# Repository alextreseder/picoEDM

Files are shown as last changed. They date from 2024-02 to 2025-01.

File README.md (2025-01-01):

# PicoEDM

Minimalist DIY Wire EDM for Hobbyists & Education. Designed with high accuracy and user experience in mind.

[**Join the Discord!!**](https://discord.gg/fNJQsGFzm4)

[**Pico Makes First Cut!**](https://youtube.com/shorts/JkDtk-GV0A8)

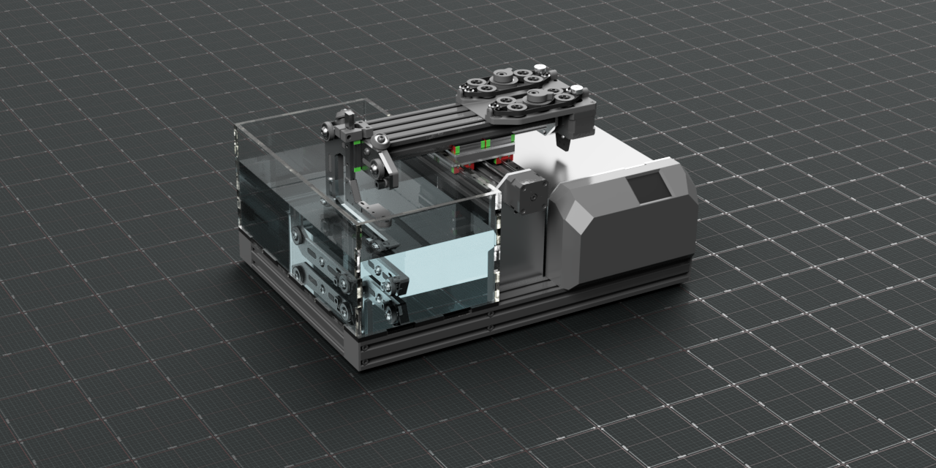
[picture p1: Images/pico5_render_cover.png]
Render Cover


## Concept

* Use components that are readily available worldwide (Amazon.com serving as benchmark)
* 360mm by 500mm footprint and 160mmX; 160mmY; 50mmZ travels
* Use a belted friction drive for wire handling
* Use a integrated driver closed loop stepper in torque mode to tension the wire
* Use inert materials for underwater assemblies
* Implement adjustable worktable for precision
* Use preloaded Tr8x2 nuts with integrated leadscrew steppers and mgn12 rails for motion
* Support the following features via a quick swap kinematic mount:
  * Sinker EDM end effector
  * Hole popper end effector

The firmware and spark generator is a seperate project supplied by
[GEDM](https://github.com/G-EDM)

## Project Status
```diff
+ PROJECT NOW IN BETA! CURRENT VERSION: PICO7
```
## Disclaimers

**EDM machines are dangerous**  
Beware electric shock and pinch points. Be prepared to activate emergency stop. Do not leave machine unattended. You are responsible for your own safety.

**Metric / Imperial**
The machine is nearly completely metric with the exception of the thickness of the laser cut parts. The nearest metric equivalents should work in all cases, but user should carefully review the CAD model before building to confirm.

## Currently In Progress

* Implement assited self threading

## Associated Projects
[NanoEDM - A higher quality machine](https://github.com/alextreseder/nanoEDM)

[KegStand - A consumables free water management system for EDM](https://github.com/alextreseder/kegstand)

## Future Goals
Future Development:
* Ultra-compact spark generator based on FGPA control technology

## Non-Goals
This is not a spark generator or firmware project, although I do have a high end spark generator under development. This is not an ultra precision machine. This is not a low precision machine.

## Calculations
Desmos calculators have been made for various applications - they are not necessarily complete

[DESMOS - CAPSTAN EQUATION](https://www.desmos.com/calculator/trg4qsopa3)

## Donations
Bitcoin address: bc1qqp8etjvsmyyjqjm5unr0l4kj4qqpekz5jcclxv

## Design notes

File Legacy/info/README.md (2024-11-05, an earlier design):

# Bill Of Materials

## Fabricated Parts

|Part |Source |QTY  |Cost Each |Cost Each (Bulk) |
|---|---|-----|---|---|
|Preload Nut Mount |SendCutSend|2 |$2 |$0.50 |
|Tank Floor Thick Plate|SendCutSend|1 |$66 |$16.00 |
|Tank Floor Thin Plate |SendCutSend|1 |$28 |$7 |
|Wire Frame |SendCutSend|1 |$40 |$12 |
|X Axis Plate |SendCutSend|2 |$18 |$6.00 |
|Tank Walls |Home Laser |1 |$20.00 |$5.00 |
| | | | | |
| | |total|194 |53 |

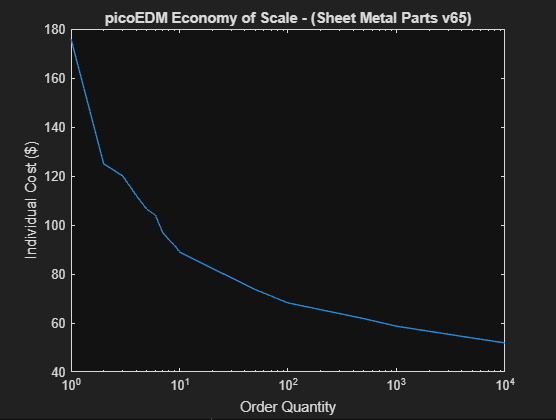
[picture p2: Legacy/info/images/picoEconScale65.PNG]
Economy of Scale


## Sourced Parts

|Part |Source |QTY  |Cost Each |Cost Each (Bulk) |Link|
|---|---|:---:|---:|---:|----|
|608zz Ceramic |Amazon |8 |$2 |$0.50 | |
|608zz Steel |Amazon |8 |$1 |$0.10 | |
|3/4" AL Angle 48" |ACE |2 |$5 |$2 | |
|4040 V-Slot 500mm |Amazon |4 |$15 |$8 | |
|12D 350L Linear Shaft |Amazon |4 |$6 |$1.50 | |
|LM12UU |Amazon |8 |$1.50 |$0.50 | |
|Nema17 Tr8x2 300mm |Amazon |2 |$25 |$10 | |
|MR105-2RS Bearing |Amazon |1 |$0.50 |$0.05 | |
|Tr8x2 Anti-Backlash Nut  |Amazon |2 |$5 |$2 | |
|BTT Dual Gear Extruder |Amazon |1 |$14 |$5 | |
|Nema17 38mm |Amazon |2 |$12 |$8 | |
|MKS Servo42D |Amazon |1 |$25 |$9 | |
|1/2" PVC SCH80 360mm |Home Depot |1 |$4 |$0.50 | |
|Teflon Bowden Kit |Amazon |1 |$12 |$2 | |
|S203 Wire Guide |Ali Express|2 |$20 |$15 | |
|Wire Contacts |Amazon |2 |$3 |$1 | |
|4D 10L Dowel Pins |Amazon |8 |$0.20 |$0.01 | |
|4D Ball Bearings |Amazon |8 |$0.20 |$0.01 | |
|16T 5B GT2 Pulley |Amazon |2 |$3 |$0.50 | |
|5D 12L Dowel Pin |Amazon |1 |$1 |$0.01 | |
|1/2" Rubber Adhesive Feet|Amazon |6 |$1 |$0.01 | |
|1Kg PETG |Amazon |1 |$20 |$15 | |
| | | | | | |
| | |total|347.7 |155.58 | |

## Total

| | 1 | Bulk |
|:----|:---:|:---:|
|Total|$541 |$208 |

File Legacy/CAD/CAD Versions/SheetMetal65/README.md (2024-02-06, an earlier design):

# STATUS

* UP TO DATE v65

# Guide

* .dxf file name = .step file name + verison number
* Nearest metric equivalent thickness is acceptable
* Recommended Supplier (States) [SendCutSend](https://sendcutsend.com/)

## Sheet Metal Table

| Part Name v65| Quantity | Material | Thickness | 
|:---|:---:|:---:|:---:|
|Preload Nut Mount|2|AL5052|0.080"|
|Tank Floor Thick Plate|1|A36|0.250"|
|Tank Floor Thin Plate|1|SS304|0.030"|
|Tank Wall Long|2|Clear Acrylic|0.250"|
|Tank Wall Short|2|Clear Acrylic|0.250"|
|Wire Frame|1|SS304|0.187"|
|X Axis Plate|2|AL5052|0.250"|

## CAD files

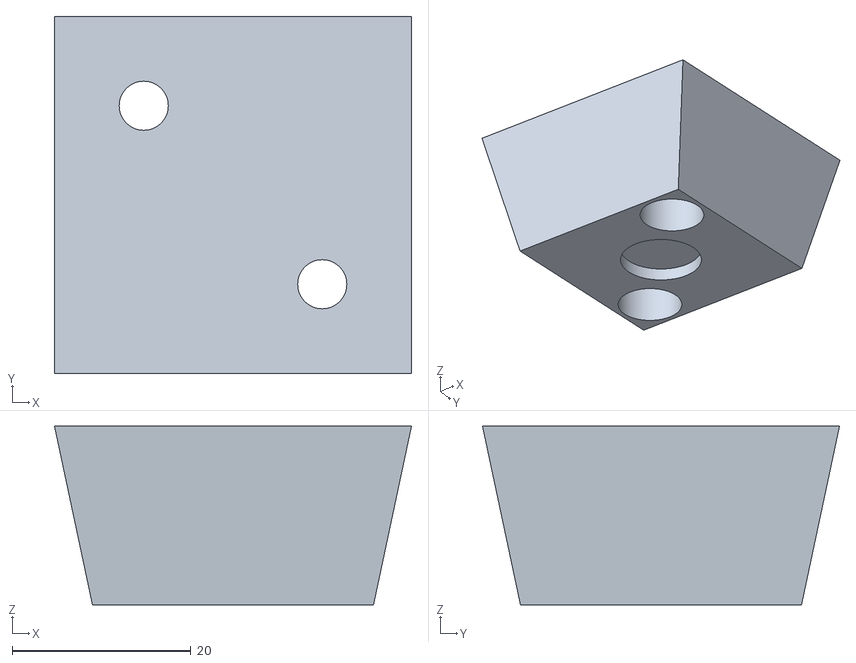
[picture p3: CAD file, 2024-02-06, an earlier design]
Legacy/CAD/CAD Versions/Prints65/MachinePrints65/FootNoHole65.stl
40.0 x 40.0 x 20.0

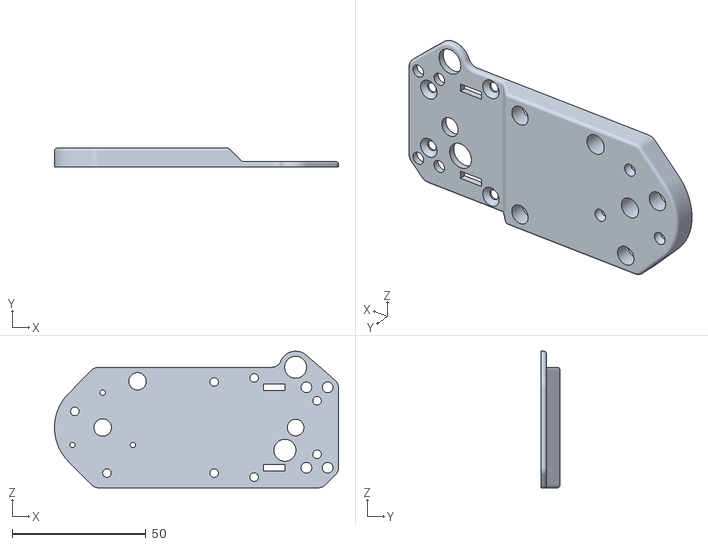
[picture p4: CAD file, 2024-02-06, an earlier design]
Legacy/CAD/CAD Versions/Prints65/WireHandlerPrints65/Bulkhead65.stl
106.0 x 7.00 x 51.0

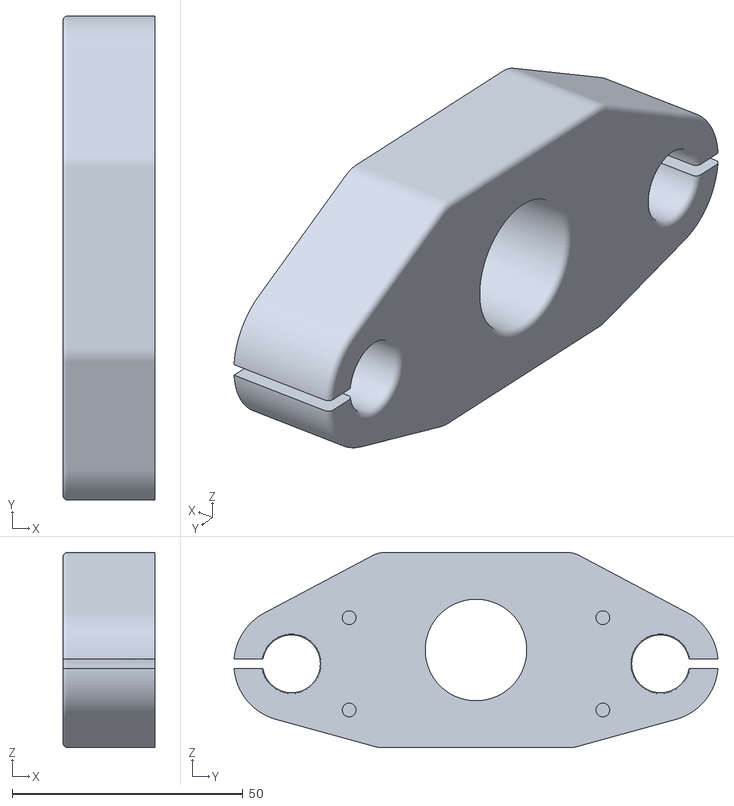
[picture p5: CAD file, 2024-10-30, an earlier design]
Legacy/CAD/CAD Versions/prints66/XbracketBearing66.stl
20.0 x 104.9 x 42.3

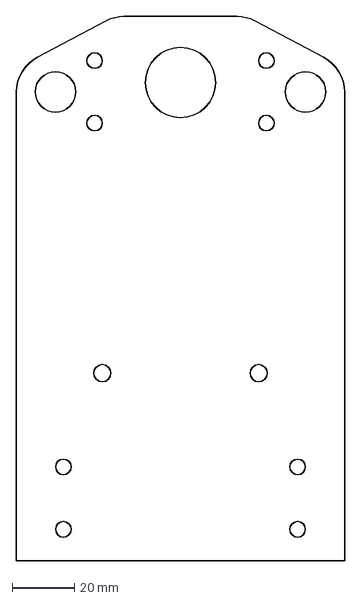
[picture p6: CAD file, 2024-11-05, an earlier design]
Legacy/CAD/CAD Versions/SheetMetal65/XaxisPlate65.dxf
105.0 x 174.2 mm

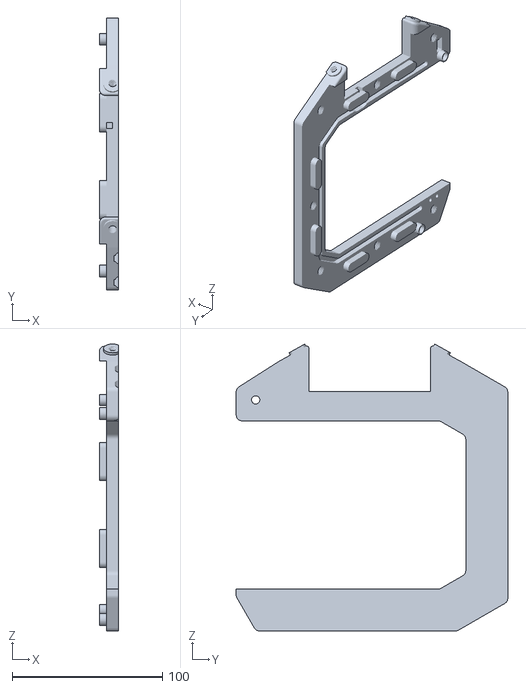
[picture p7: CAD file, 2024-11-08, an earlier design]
Legacy/pico4 prints/End Effector Frame Plastic.stl
12.8 x 181.0 x 191.2

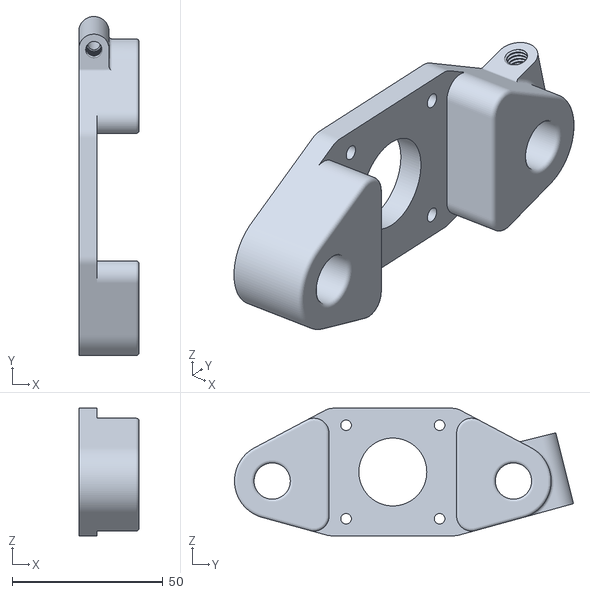
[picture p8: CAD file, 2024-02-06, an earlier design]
Legacy/CAD/CAD Versions/Prints65/MachinePrints65/XbracketMotor65.stl
20.0 x 112.4 x 42.3

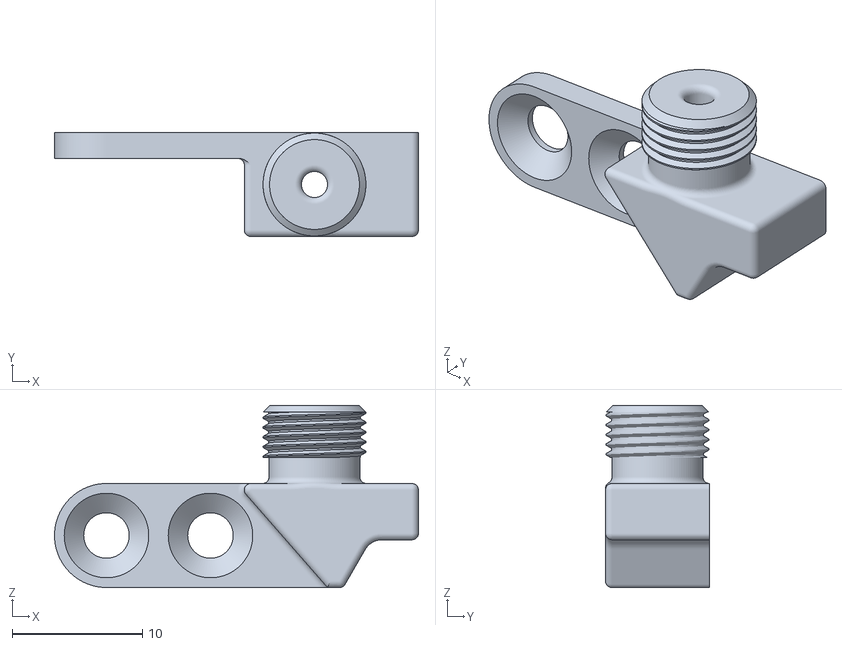
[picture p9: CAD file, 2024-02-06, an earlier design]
Legacy/CAD/CAD Versions/Prints65/WireHandlerPrints65/LowerGuideMount65.stl
28.0 x 8.00 x 14.0

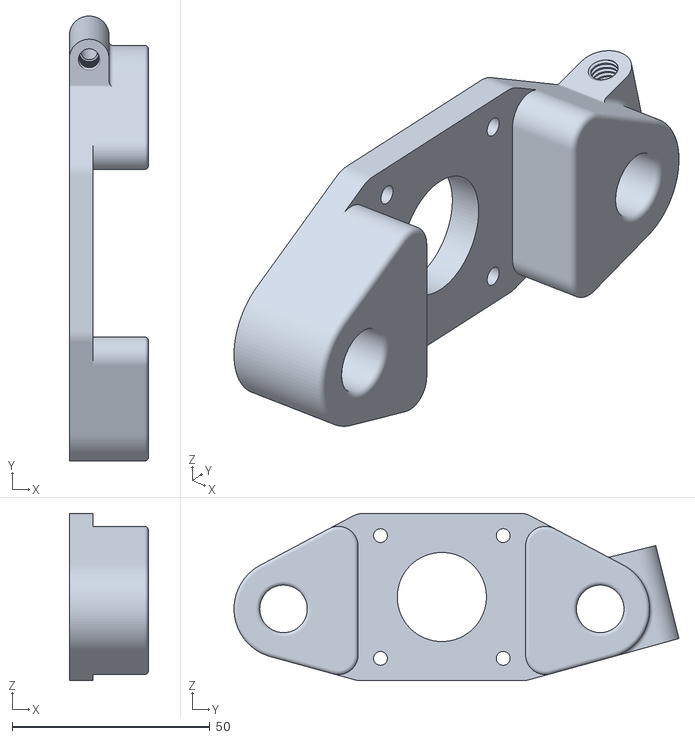
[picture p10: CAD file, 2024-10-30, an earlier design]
Legacy/CAD/CAD Versions/prints66/XbracketMotor66.stl
20.0 x 112.4 x 42.3

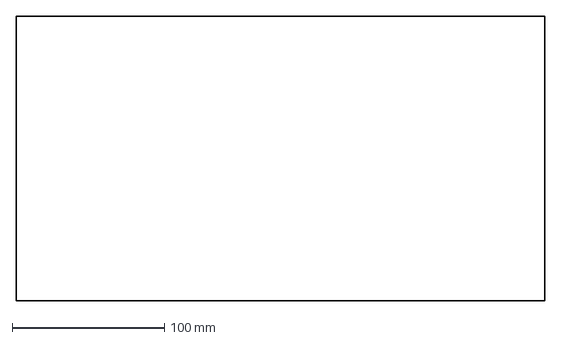
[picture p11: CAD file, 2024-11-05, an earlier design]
Legacy/CAD/CAD Versions/SheetMetal65/TankFloorThinPlate.dxf
347.0 x 187.0 mm

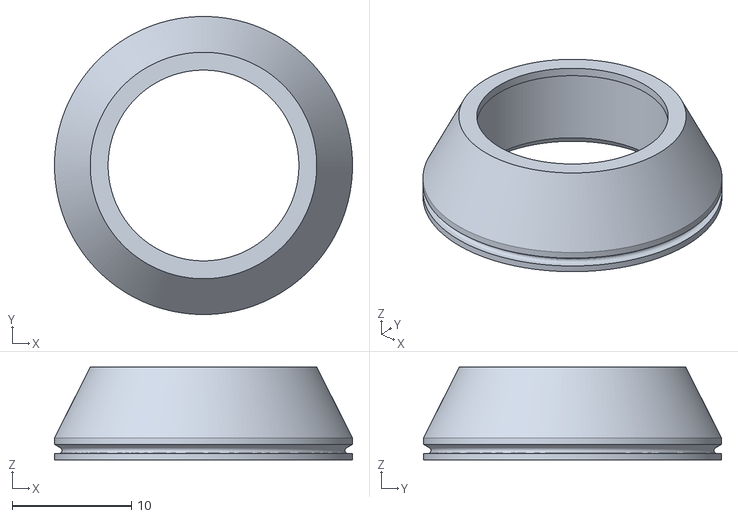
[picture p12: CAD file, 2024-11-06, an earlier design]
Legacy/pico4 prints/606 Groove Ring.stl
25.0 x 25.0 x 7.80

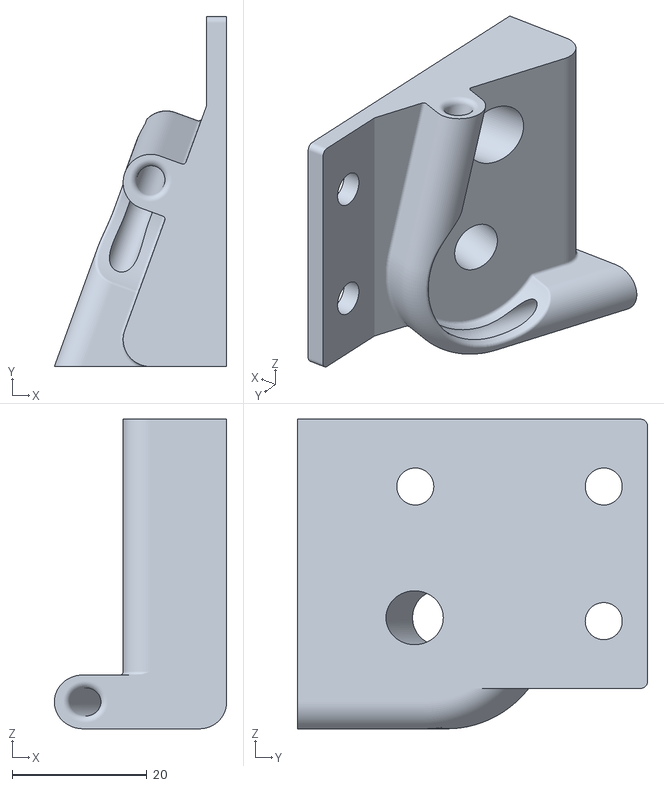
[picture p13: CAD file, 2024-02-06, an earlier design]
Legacy/CAD/CAD Versions/Prints65/MachinePrints65/UnspoolGuideSide65.stl
25.6 x 52.0 x 46.0

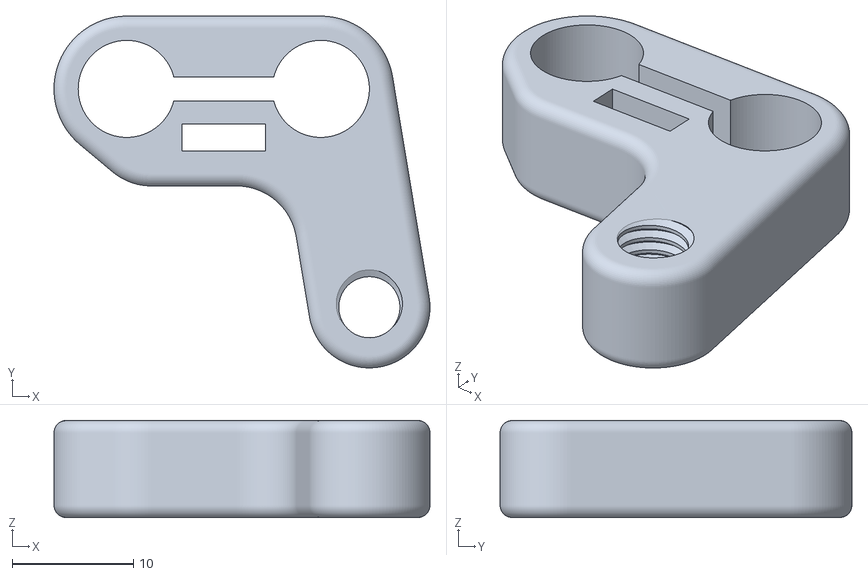
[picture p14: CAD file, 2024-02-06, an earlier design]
Legacy/CAD/CAD Versions/Prints65/WireHandlerPrints65/ZtopConnector65.stl
31.0 x 29.0 x 8.00

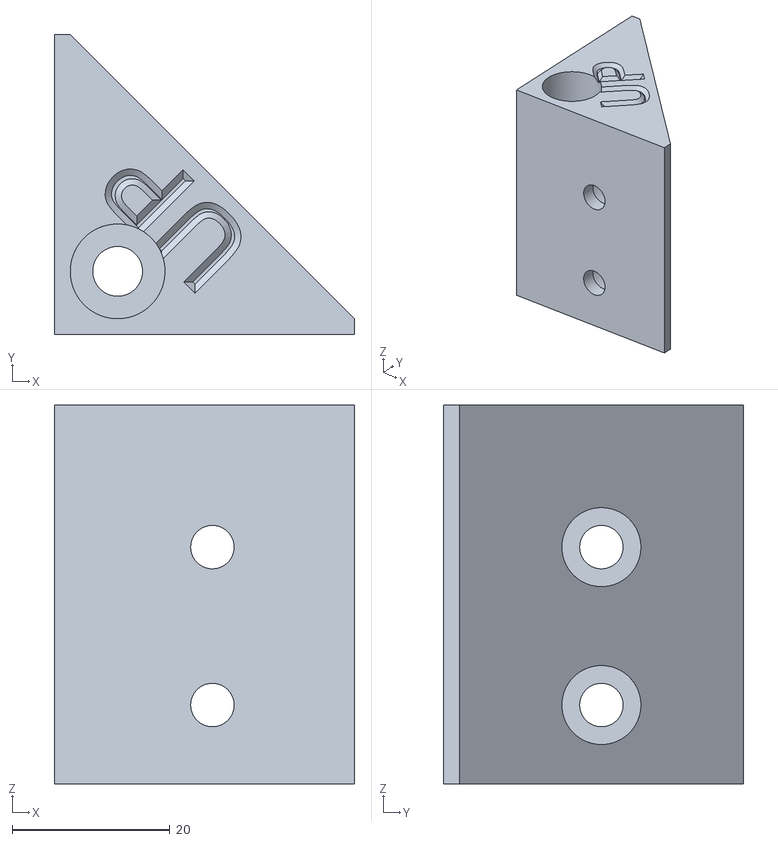
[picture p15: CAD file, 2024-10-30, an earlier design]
Legacy/CAD/CAD Versions/prints66/CornerBrace66.stl
38.0 x 38.0 x 48.0

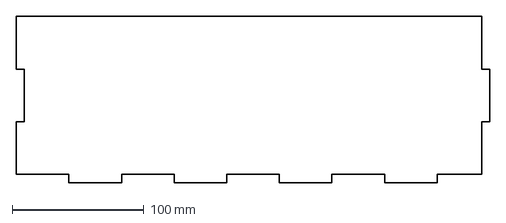
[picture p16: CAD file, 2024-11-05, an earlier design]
Legacy/CAD/CAD Versions/SheetMetal65/TankWallLong.dxf
360.0 x 126.3 mm

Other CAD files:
Legacy/pico4 prints/Lower Guide Mount.stl
Legacy/CAD/CAD Versions/Prints65/MachinePrints65/Xblock65.stl
Legacy/CAD/CAD Versions/Prints65/WireHandlerPrints65/UpperGuideMount65.stl
Legacy/CAD/CAD Versions/SheetMetal65/TankWallShort65.dxf
Legacy/CAD/CAD Versions/Prints65/MachinePrints65/CornerBrace65.stl
Legacy/CAD/CAD Versions/Prints65/MachinePrints65/ExtrusionEndCap65.stl
Legacy/CAD/CAD Versions/Prints65/MachinePrints65/FootWithHole65.stl
Legacy/CAD/CAD Versions/Prints65/MachinePrints65/KinematicCoupler65.stl
Legacy/CAD/CAD Versions/Prints65/MachinePrints65/SpoolBearingHolder65.stl
Legacy/CAD/CAD Versions/Prints65/MachinePrints65/SpoolShaftFixedEnd65.stl
Legacy/CAD/CAD Versions/Prints65/MachinePrints65/SpoolShaftFrontCap65.stl
Legacy/CAD/CAD Versions/Prints65/MachinePrints65/SpoolShaftRemovableEnd65.stl
Legacy/CAD/CAD Versions/Prints65/MachinePrints65/UnspoolGuideFront65.stl
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

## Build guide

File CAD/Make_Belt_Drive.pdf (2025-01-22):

## Pitch line: imaginary line within the belt used for calculations. Pitch is like the line that would

remain if the belt was infinitely thin.

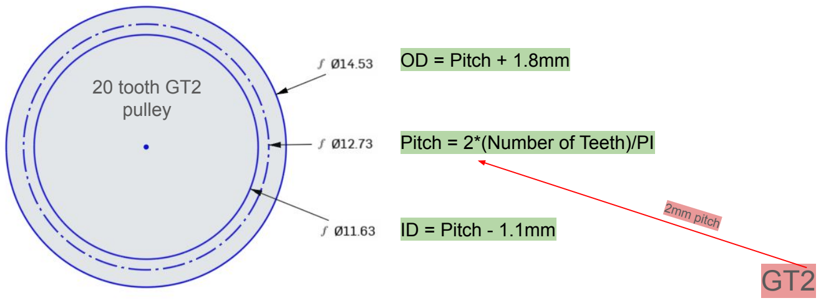
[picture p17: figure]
Pitch = 2*(Number of Teeth)/PI; OD = Pitch + 1.8mm; ID = Pitch - 1.1mm; 20 tooth GT2 pulley; 2mm pitch

## Pitch diameter is not in the middle of the OD and ID. 1.8mm and 1.1mm are typical measured values for GT2 belts

## Since we know there are 20 teeth on the pulley with 2mm pitch, then the pitch circumference is 40mm. If we want to use a 100mm (50

tooth) belt, the distance between centers needs to be 30mm.

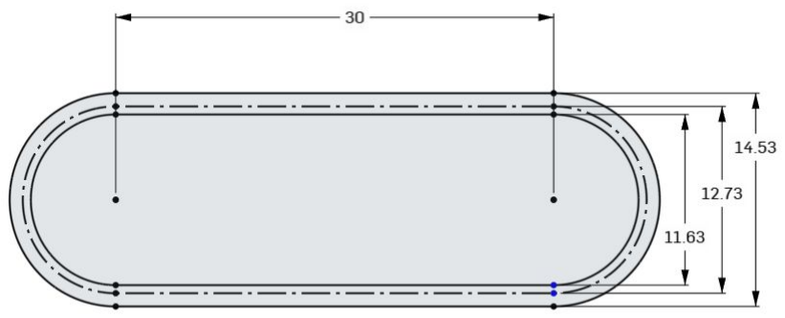
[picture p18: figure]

## 40mm + 30mm + 30mm = 100mm This method is not scalable for more complex configurations

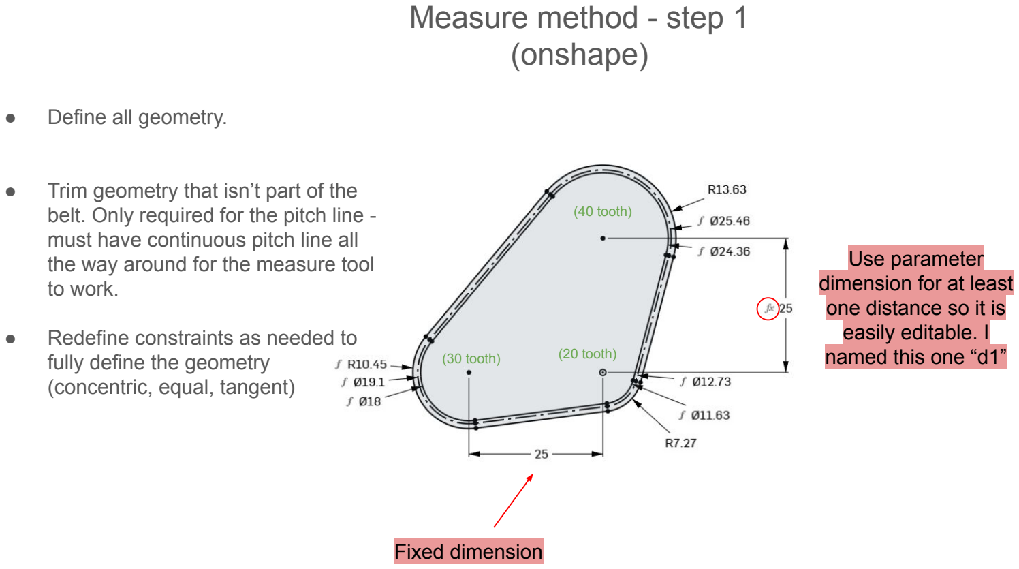
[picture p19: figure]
Measure method - step 1 (onshape); ● Define all geometry.; ● Trim geometry that isn’t part of the; must have continuous pitch line all the way around for the measure tool to work.; ● Redefine constraints as needed to fully define the geometry (concentric, equal, tangent); (40 tooth); (30 tooth); (20 tooth); Fixed dimension; Use parameter dimension for at least one distance so it is easily editable. I named this one “d1”

belt. Only required for the pitch line -

## Measure method - step 2 (onshape)

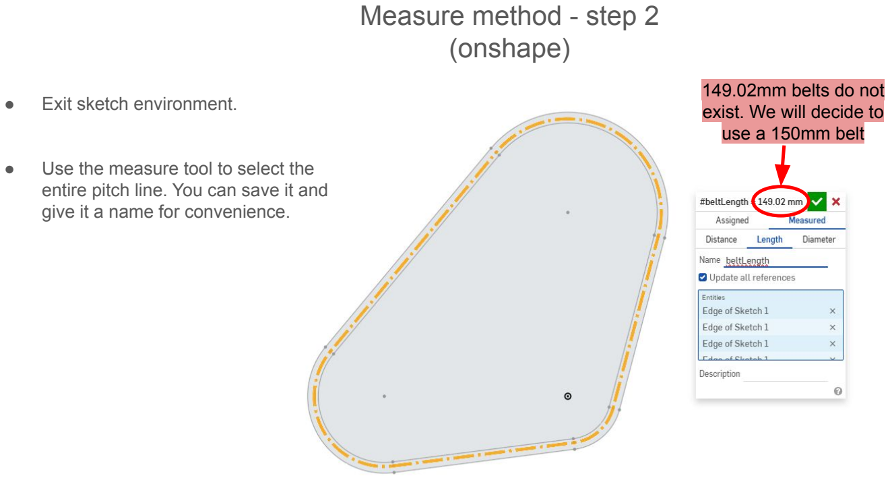
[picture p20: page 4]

- Exit sketch environment.
- Use the measure tool to select the entire pitch line. You can save it and give it a name for convenience.
| | 149.02mm belts do not
exist. We | will decide to
use a 150mm belt

## Measure method - step 3 (onshape)

- Adjust the parameter dimension by trial and error until the measured belt length is within 0.001mm of the desired belt length

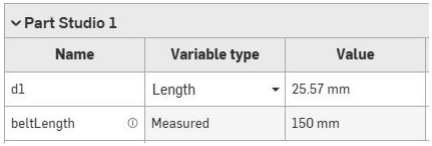
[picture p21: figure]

## Back to back belts

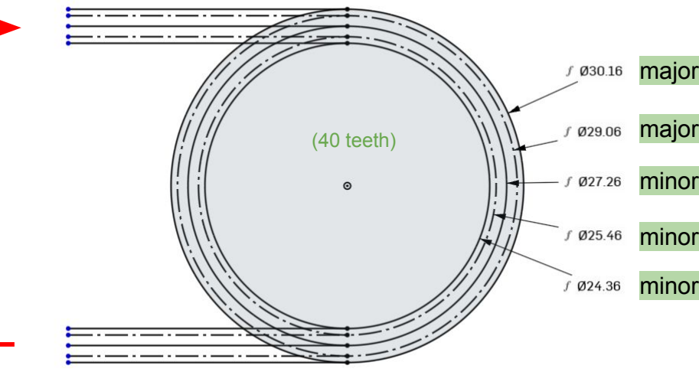
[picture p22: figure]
(40 teeth)

majorOD = minorPitch + 4.7mm

majorPitch = minorPitch + 3.6mm

minorOD = minorPitch + 1.8mm

minorPitch = 2*(Number of teeth)/PI

minorID = minorPitch - 1.1mm

## Complication #1 - Problem

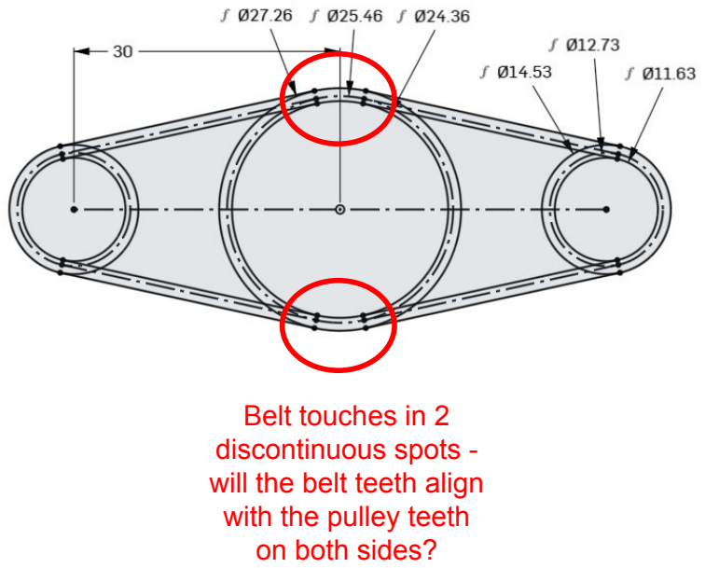
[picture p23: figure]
Belt touches in 2 discontinuous spots - will the belt teeth align with the pulley teeth on both sides?

## Complication #1 - Solution

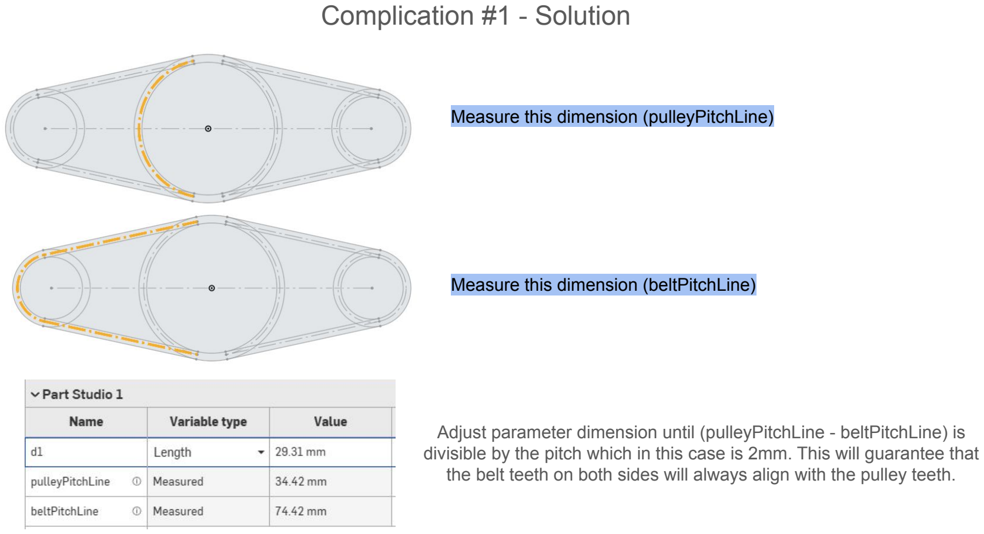
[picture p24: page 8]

Measure this dimension (pulleyPitchLine)

Measure this dimension (beltPitchLine)

Adjust parameter dimension until (pulleyPitchLine - beltPitchLine) is divisible by the pitch which in this case is 2mm. This will guarantee that the belt teeth on both sides will always align with the pulley teeth.

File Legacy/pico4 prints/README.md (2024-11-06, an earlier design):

|Part |QTY|
|---|---|
|40T Pulley |8  |
|60T Pulley |2  |
|606 Groove Ring |2  |
|608 Groove Ring |4  |
|Belt Drive Frame |1  |
|Contact insulator |2  |
|Drag Chain Bracket |1  |
|Eccentric Pin |2  |
|End Effector Frame Plastic |1  |
|Extrusion Cap |4  |
|Flex Tensioner |1  |
|Lower Guide Mount |1  |
|Upper Guide Mount |1  |
|XY Connector Riser |1  |
|Z Rails Top Connector |1  |

All parts: black ABS ideal, 0.15mm layer height recommended

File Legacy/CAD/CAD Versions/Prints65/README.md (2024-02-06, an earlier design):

# STATUS

* UP TO DATE v65

# Guide

* .stl file name = .step file name + verison number
* PETG or ABS recommended

## Machine Print Table

| Part Name v65| Quantity | Layer Height |
| :--- |:---:| :---:|
|Corner Brace|4|0.2|
|Extrusion End Cap|4|0.2|
|Foot No Hole|5|0.2|
|Foot With Hole|1|0.2|
|Kinematic Coupler|1|0.2|
|Spool Bearing Holder|2|0.2|
|Spool Shaft Fixed End|1|0.2|
|Spool Shaft Front Cap|1|0.2|
|Spool Shaft Removable End|1|0.2|
|Unspool Guide Front|1|0.2|
|Unspool Guide Side|1|0.2|
|X Axis Plate Gusset|2|0.2|
|X Block|1|0.2|
|X Bracket Bearing|1|0.2|
|X Bracket Motor|1|0.2|
|Y Block|1|0.2|
|Y Bracket Motor|1|0.2|

## Wire Handler Print Table

| Part Name v65| Quantity | Layer Height |
| :--- |:---:| :---:|
|Brake Motor Mount|1|0.15|
|Bulkhead|1|0.15|
|Capstan Wheel|1|0.15|
|Groove Wheel Low|1|0.15|
|Groove Wheel Middle|5|0.15|
|Lower Guide Mount|1|0.15|
|Upper Guide Mount|1|0.15|
|Z Clamp|1|0.15|
|Z Top Connector|1|0.15|

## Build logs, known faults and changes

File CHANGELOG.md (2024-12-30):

## Change Log
Version 7 (current) adds the following features:
* Fixed minor issues

Verison 6 (legacy) adds the following features: 
* Integrated electronics case
* Improved belt drive tensioning scheme

Verison 5 (legacy) adds the following features: 
* mgn rails
* belted drive
* new end effector

Verison 65 (legacy) adds the following features:
* Stepper brake pulley changed to 16 tooth
* Stepper brake mount geometry improved
* Magentetic kinematic coupler changed to bolted kinematic coupler. Magnet will be revisited
* Wire unspooling path components are  now modeled
* Machine now includes all features needed to run comfortably
* Project status updated to beta

Verison 62 (legacy) adds the following features (huge changes):
* Capstan brake changed from rotary damper brake to stepper motor brake via MKS Servo42D driver in torque mode
* All heat set thread inserts removed in favor of plastic screws 
* Redesigned wire end effector Z axis slider for better stability
* Doubled up the coupling magents to hold the end effector on better
* Again: Re-jointed the entire model from step files to clean things up and eliminate worthless dependancies
* Changed workholding strategy to magnetic base plate in tank. Any fixtures you want can be printed and attached with magnets

Verison 59 (legacy) adds the following features:
* Redesigned wire end effector Z axis slider to eliminate the need for milling
* Re-jointed the entire model from step files to clean things up and eliminate worthless dependancies
* Fixed subtle issues with water tank bumper geometry
* .f3d file now available
* Capstan bearings and shaft switched from 1/4" to M6 and 6x12x4 bearing

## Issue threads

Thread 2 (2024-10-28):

documentation on brake

Cncninja, 2024-10-28:
I'm building the pico and don't understand how the brake is making drage it has a stepper connected is the stepper shorted to cause drag? or is it under driven vs the respooler.

alextreseder, 2024-10-30:
Braking is accomplished with an integrated closed loop driver that is capable of a sort of pseudo-"torque mode" that works plenty well enough with not too much cogging. We basically use a stepper motor to emulate an adjustable rotary damper. Ideally, this means the motor driver tries to keep the velocity at 0 with some allowable torque limit.

MKS s42c works for the torque effect but it is not possible to set the velocity to 0. That means you have to have it try to hold a position, so if your wire breaks, the motor will spin all the way back to position 0 which is a nuisance. This is a firmware problem but the firmware is not open source.

CLN17 v2 from creapunk should be the fix for this. However, they are still in beta testing and a little hard to get your hands on. I recommend you use the MKSs42c for now, put a button on the power source so you can reset the device if the wire breaks.

Cheers

alextreseder, 2024-10-30:
Ill add this to the documentation when the new version goes fully live

Closed 2024-12-30.

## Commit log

2024-01-28 new cad release
2024-02-06 Create cad
2024-02-06 add CAD version
2024-11-05 update files
    [BrakeMotorMount65.stl, Bulkhead65.stl, CapstanWheel65.stl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]
2024-11-06 add print files
    [40T Pulley.stl, 606 Groove Ring.stl, 608 Groove Ring.stl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]
2024-12-30 new version
    [40T Pulley.stl, 606 Groove Ring.stl, 608 Groove Ring.stl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]
